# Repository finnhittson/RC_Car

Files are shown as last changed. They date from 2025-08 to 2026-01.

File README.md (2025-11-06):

# 9V Battery Power RC Car
This repo documents how to make an RC car and transmitter using 3D printted parts, a PIC16LF18325 microcontroller, nRF24L01 RF modules, a 9V battery to power the car and the transmitter, and other basic hardware components.

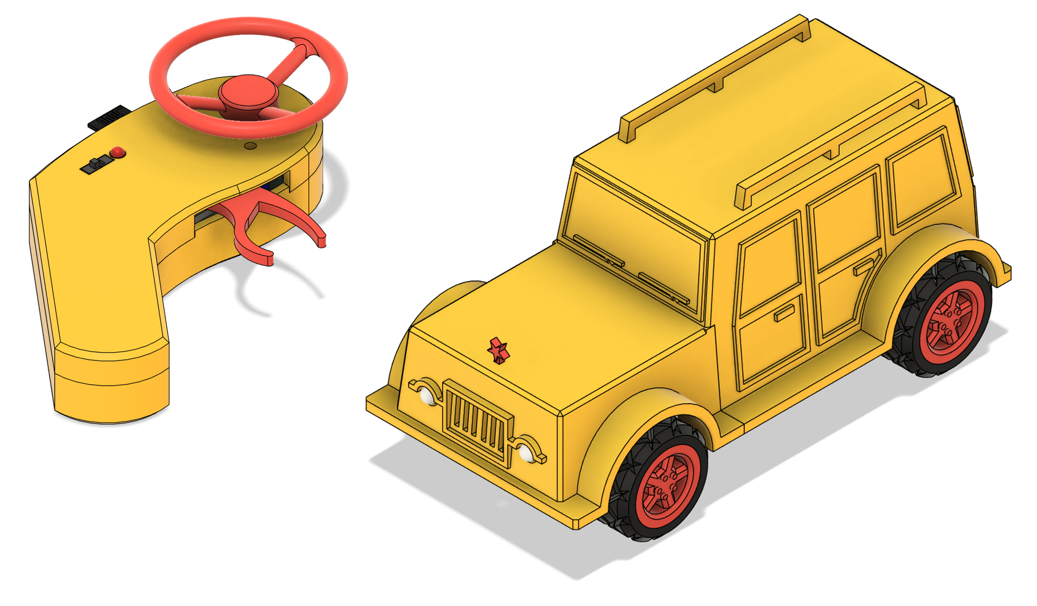
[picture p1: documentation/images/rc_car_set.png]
RC_Car


Table of contents:  
1. [Design Overview](##design-overview)
2. [Software](###software)
3. [Electrical](###electrical)
4. [Bill of Materials](##bill-of-materials)
## Design Overview
The three main components in building this car are the software, electrical, and the mechanical aspect of the car and controller. The following sections talks about each of these parts in detail.

### Software
Using the PIC16LF18326 as the microcontroller, the driver code was written exclusively in C. The driver code was programmed onto the PIC16 using the MPLAB SNAP and the MPLABX IDE. The software components are broken into the following three files:
1. `main.c`: runs main finite state machine responsible for executing high level transmitter/receiver instructions for controlling motors and servos for the receiver and reading analog control inputs for the trasmitter.
2. `spi.c`: helper SPI functions for transmitting and receiving messages to and from the nRF24L01 radio module.
3. `nRF24L01.c`: helper functions for configuring the nRF24L01 radio module using the `spi.c` functons.

Because this project is intended to be a workshop only one version of code or `main.c` file is written for simplicity. Therefore, for the `main.c` to differentiate between running transmitter code and receiver, a GPIO pin on the micro is dedicated for this indication. The pin under questions is RA5 (pin 2) from the tables below which descripe the pinout for the PIC16 in both the receiver and transmitter. If RA5 is pulled high, then the `main.c` executes transmitter code only. Similarly if RA5 is pulled low, then the `main.c` only executes receiver code. 

| Transmitter Pin Description | | | | | | Receiver Pin Description | | | |
|---|---|---|---|-|-|---|---|---|---|
| **Pin Number** | **Port** | **Net Name** | **Notes** | | | **Pin Number** | **Port** | **Net Name** | **Notes** |
| 1 | $V_{DD}$ | 3.3V | power supply | | | 1 | $V_{DD}$ | 3.3V | power supply |
| 2 | RA5 | 3.3V | type select | | | 2 | RA5 | GND | type select |
| 3 | RA4 | CSN | SPI bus | | | 3 | RA4 | CSN | SPI bus |
| 4 | RA3 | MCLR | program/NC | | | 4 | RA3 | MCLR | program/NC |
| 5 | RC5 | MOSI | SPI bus | | | 5 | RC5 | CE | radio enable |
| 6 | RC4 | SPEED | pot input | | | 6 | RC4 | PWM5.1 | motor PWM |
| 7 | RC3 | STEER | pot input | | | 7 | RC3 | PWM6 | servo PWM |
| | | | | | | | | | |
| 8 | RC2 | IRQ | radio interrupt | | | 8 | RC2 | PWM5 | motor PWM |
| 9 | RC1 | MISO | SPI bus | | | 9 | RC1 | MISO | SPI bus |
| 10 | RC0 | SCK | SPI bus | | | 10 | RC0 | SCK | SPI bus |
| 11 | RA2 | CE | radio enable | | | 11 | RA2 | MOSI | SPI bus |
| 12 | RA1 | STEER_TRIM | pot input | | | 12 | RA1 | IRQ | radio interrupt |
| 13 | RA0 | LED | status | | | 13 | RA0 | LIGHTS | status |
| 14 | $V_{SS}$ | GND | power supply | | | 14 | $V_{SS}$ | GND | power supply |

The following image shows the state machine executed on the transmitter PIC16. When the PIC16 detects its a transmitter then it starts the state machine with the inital state of *COLLECT_ADC_DATA*. In the *COLLECT_ADC_DATA* state, the PIC16 cycles through the three ADC ports to collect their value. Once complete, it transitions to the *TRANSMIT_ADC_DATA* state where it packages up this information into a packet and sents this information over the SPI bus to the nRF24L01 radio module. Once this is complete it then transitions to the *CLEAR_INTERRUPT* state. In this state the PIC16 is waiting for the interrupt line to go low which indicates a successful transmission to the receiver. From here the state machine then transitions to a *DONE* state where the hardware to read the analog pins is reinitialized and the process repeates itself after *DONE* transitions to *COLLECT_ADC_DATA*.

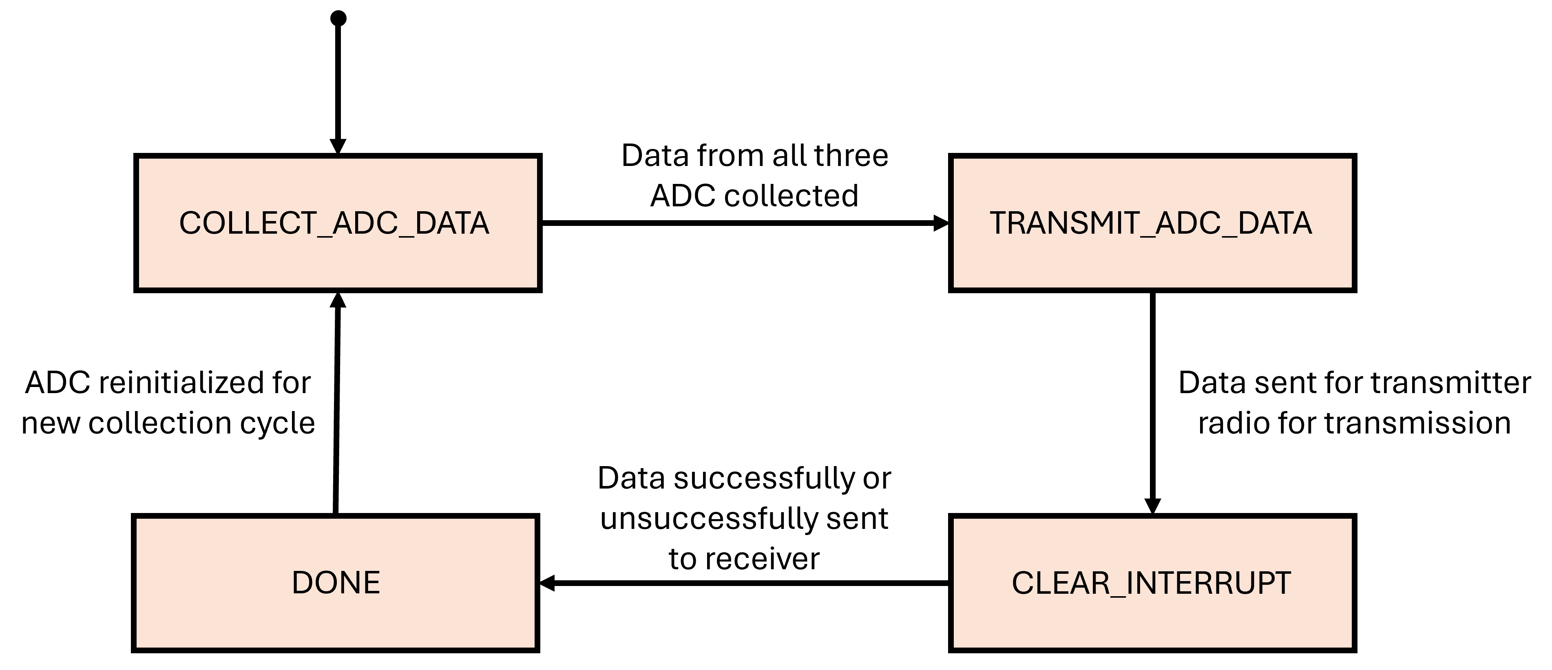
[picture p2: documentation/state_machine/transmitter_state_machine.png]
Transmit_state_machine


The transmission packet is 8 bytes long and has the following breakdown.
1. Byte 1 is the radio ID and is chosen by the user as an extra indentification method so that in the instance when the radio receives a packet from another RC car on the same channel, it will only execute the instructions if the packet come from a transmitter with the same ID.
2. Byte 2 is the high byte of the ADC conversion value for RC4. The PIC16 has a 10 bit ADC so it takes two bytes to store its value. It stores the eight LSB of the conversion in the first byte and the remaining two bits in the first two bits of the second byte.
3. Byte 3 is the low byte of the ADC conversion value for RC4.
4. Byte 4 is the high byte of the ADC conversion value for RC3.
5. Byte 5 is the low byte of the ADC conversion value for RC3.
6. Byte 6 is the high byte of the ADC conversion value for RA1.
7. Byte 7 is the low byte of the ADC conversion value for RA2.
8. Byte 8 is a checksum of all the bytes transmitted. The checksum is computed by summing all the bytes and subtracting the result from 0xFF. The result is transmitted and the receiver checks the checksum by summing every byte of the packet and if the result is 0xFF then no bits were corrupted or lost.

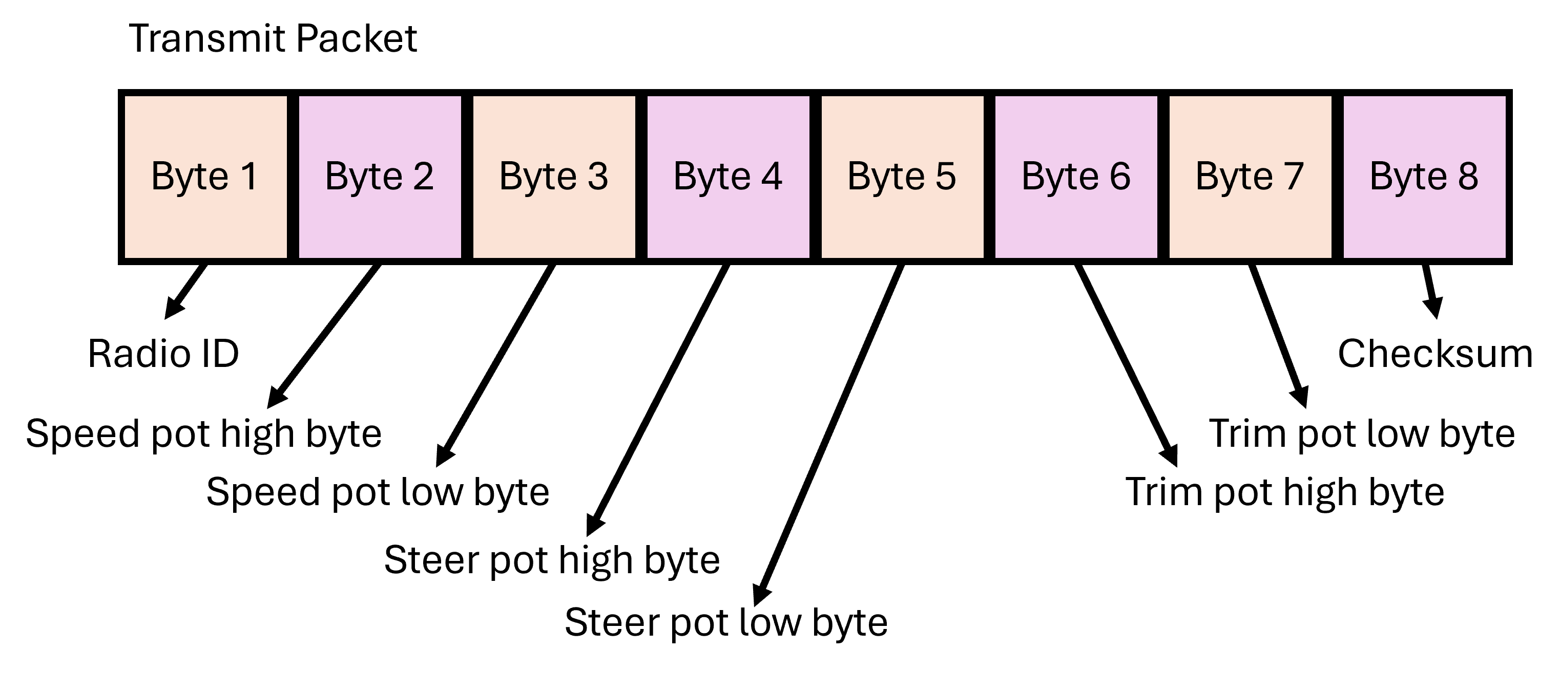
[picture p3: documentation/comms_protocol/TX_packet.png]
Packet_structure


When the PIC16 detects is a receiver it starts the state machine in the *READ_RX*. In this state it waits until the interrupt line from the nRF24L01 radio module goes low which indicates that a packet has been received. From here it transitions to the *UPDATE_CONTROLS* state. In this state the PIC16 collects the packet from the nRF24L01 radio module, unpacks it, and updates the PWM signals for the servo and motor. Once complete it transitions back to the *READ_RX* state where it waits until the next packet is ready.

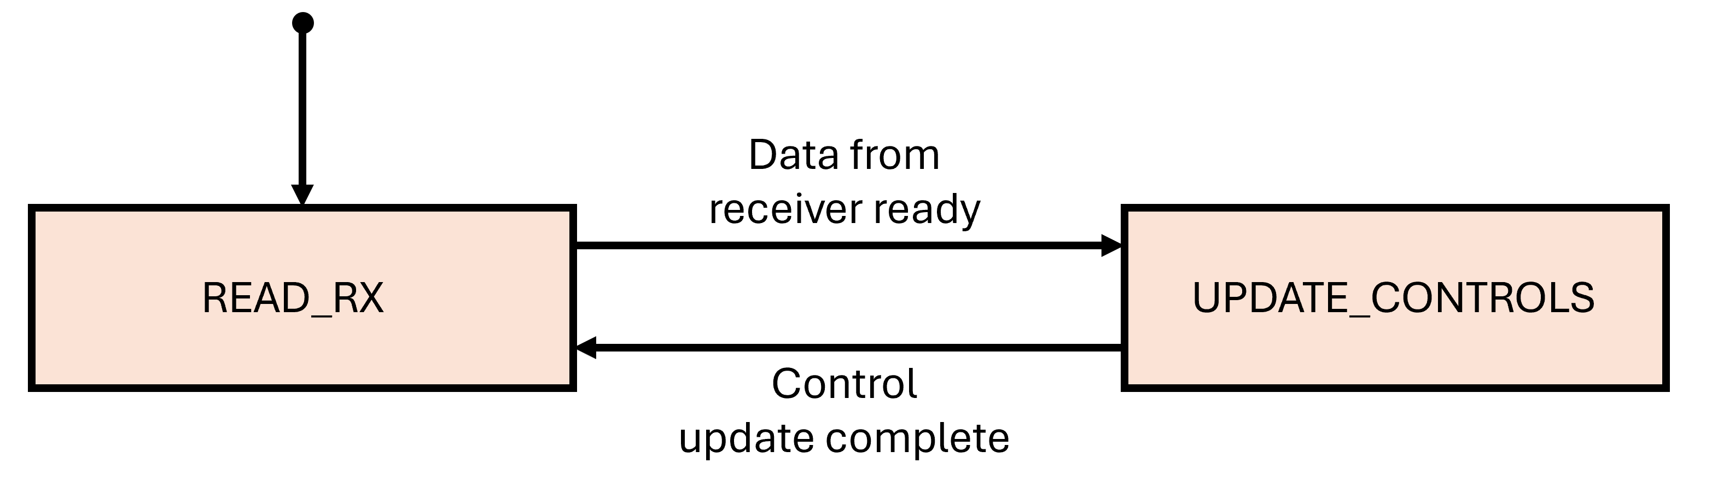
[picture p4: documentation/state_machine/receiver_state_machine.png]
Receive_state_diagram

### Electrical
The receiver schematic is shown below. For the receiver, the PIC16LF18325 communicates with the nRF24L01 radio module through a SPI bus for receiving commands that are then decoded into a PWM signals for motor and servo control. The PIC16 also controls the motors and servo respectivly and was chosen for its small size, GPIO pin count, and packaging style. The L9110 h-bridge controls the motor and is a very basic h-bridge for driving small motors which make it perfect for this application. The LM2937 linear voltage regulator creates the 3.3V supply for the PIC16, nRF24L01 radio module, lights, and servo power. The lights part of the schematic act as the headlights of the car and are controlled by the PIC16 toggeling the 2N7000 mosfets. 
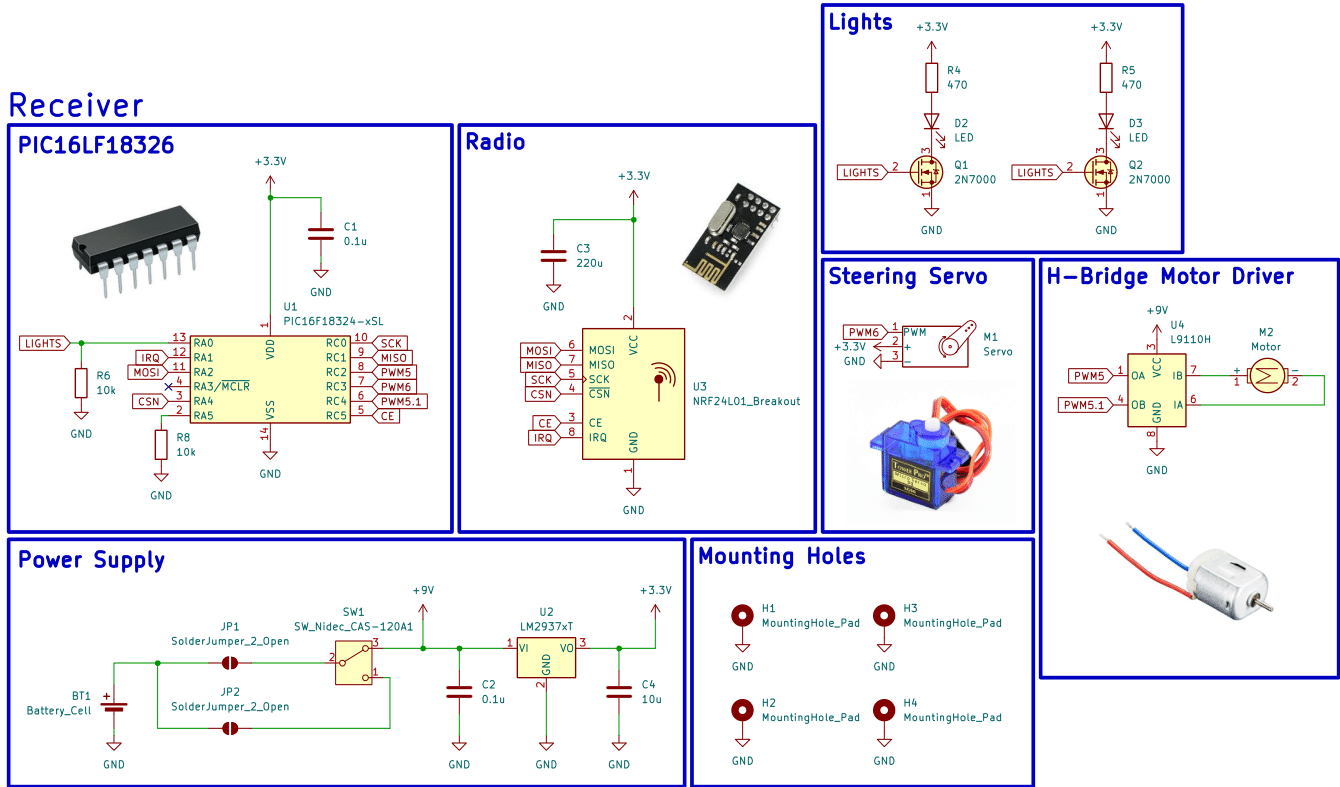
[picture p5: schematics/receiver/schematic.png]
Receiver_schematic


The transmitter schematic is shown below. In this instance the PIC16 commuicates with the nRF24L01 radio module to send commands for the receiver. The PIC16 also controls the status LED which indicates power and pairing status. The two modes of control are the two potentiometers which act as the cars accelerator and steering control. There is also one trim pot for the driver to tune the front steering axel so that the car does not drift left or right when driving straight.

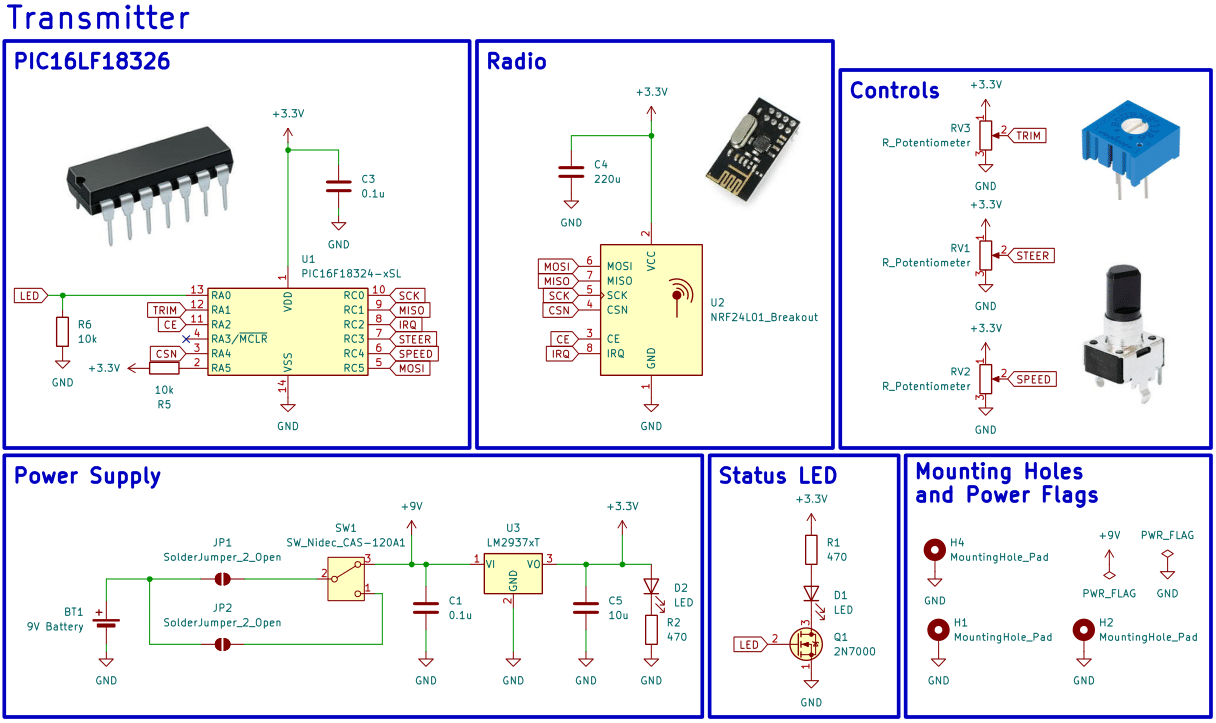
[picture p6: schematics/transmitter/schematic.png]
Transmitter_schematic


### Mechanical

## Bill of Materials
| Transmitter Bill of Materials | | | |
|---|---|---|---|
| **Component** | **Quantity** | **Source** | **Part Number** |
| 9V battery | 1 | DigiKey | 547-A1604BK210J-ND |
| 0.1uF | 2 | DigiKey | BC1084TR-ND |
| 220uF | 1 | DigiKey | 399-6122-ND |
| 10uF | 1 | DigiKey | 399-15738-ND |
| LED | 2 | DigiKey | 732-5016-ND |
| 2N7000 | 1 | DigiKey | 4878-2N7000CT-ND |
| 470 | 2 | DigiKey | CF14JT470RTR-ND |
| 10k | 2 | DigiKey | CF14JT10K0TR-ND |
| 5k Control Pot | 2 | DigiKey | 2223-PT01-D115D-B502-ND |
| 5k Trim Pot | 1 | DigiKey | 3386P-103LF-ND |
| Power Switch | 1 | DigiKey | EG1903-ND |
| PIC16LF18326 | 1 | DigiKey | PIC16LF18326-I/P-ND |
| nRF24L01 Radio Module | 1 | AliExpress | [nRF24L01](https://www.aliexpress.us/item/3256809251216534.html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) |
| LM2937 | 1 | DigiKey | LM2937ET-3.3/NOPB-ND |

| Receiver Bill of Materials | | | |
|---|---|---|---|
| **Component** | **Quantity** | **Source** | **Part Number** |
| 9V battery connector | 1 | DigiKey | 547-A1604BK210J-ND |
| 0.1uF | 2 | DigiKey | BC1084TR-ND |
| 220uF | 1 | DigiKey | 399-6122-ND |
| 10uF | 1 | DigiKey | 399-15738-ND |
| LED | 2 | DigiKey | 732-5016-ND |
| 9g Servo | 2 | DigiKey | 732-5016-ND |
| 2N7000 | 1 | DigiKey | 4878-2N7000CT-ND |
| 470 | 2 | DigiKey | CF14JT470RTR-ND |
| 10k | 2 | DigiKey | CF14JT10K0TR-ND |
| Power Switch | 1 | DigiKey | EG1903-ND |
| PIC16LF18326 | 1 | DigiKey | PIC16LF18326-I/P-ND |
| nRF24L01 Radio Module | 1 | AliExpress | [nRF24L01](https://www.aliexpress.us/item/3256809251216534.html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) |
| LM2937 | 1 | DigiKey | LM2937ET-3.3/NOPB-ND |
| L9110H | 1 | DigiKey | 1528-4489-ND |

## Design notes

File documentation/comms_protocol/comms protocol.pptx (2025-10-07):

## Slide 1

Transmit Packet

Byte 1

Radio ID

Byte 2

Byte 3

Byte 4

Byte 5

Byte 6

Byte 7

Byte 8

Checksum

Speed pot high byte

Speed pot low byte

Trim pot high byte

Trim pot low byte

Steer pot high byte

Steer pot low byte

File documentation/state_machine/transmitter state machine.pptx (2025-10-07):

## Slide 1

COLLECT_ADC_DATA

Data from all three
ADC collected

TRANSMIT_ADC_DATA

ADC reinitialized for
new collection cycle

Data sent for transmitter
radio for transmission

DONE

Data successfully or
unsuccessfully sent
to receiver

CLEAR_INTERRUPT

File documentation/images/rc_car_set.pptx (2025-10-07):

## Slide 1

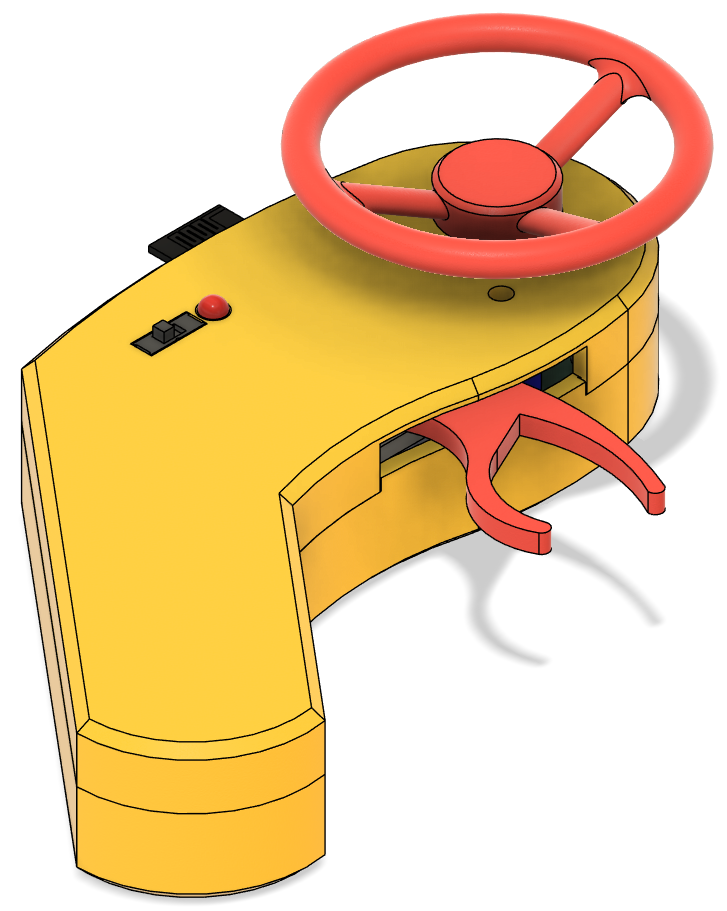
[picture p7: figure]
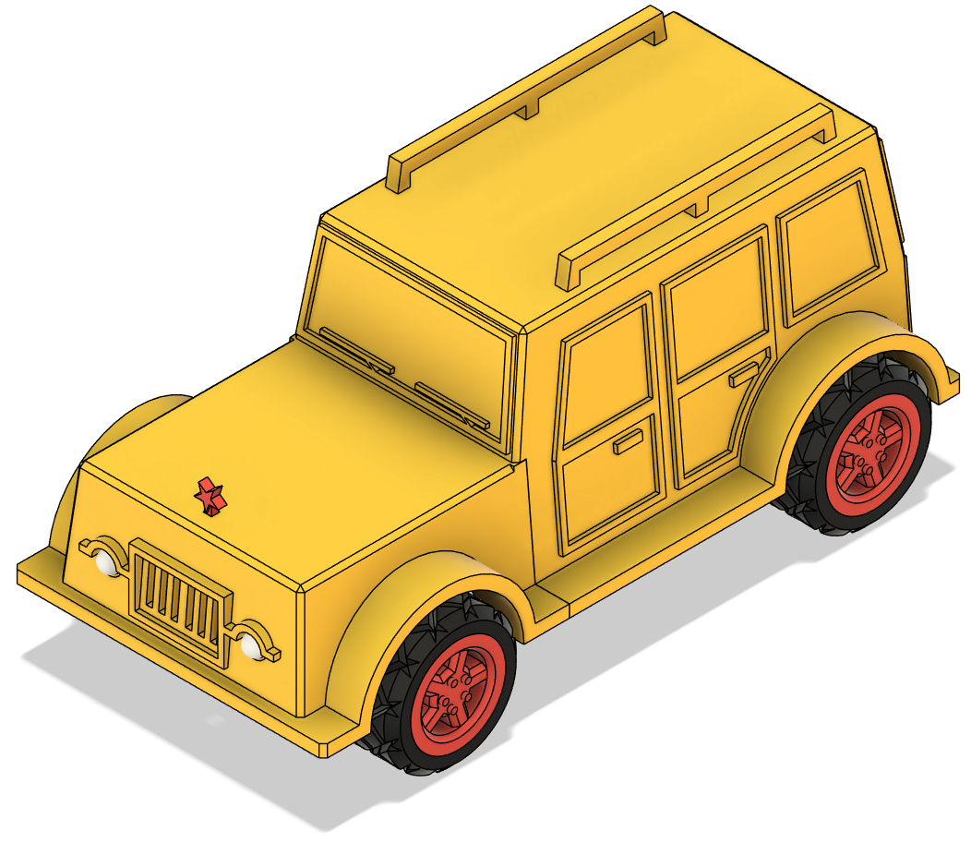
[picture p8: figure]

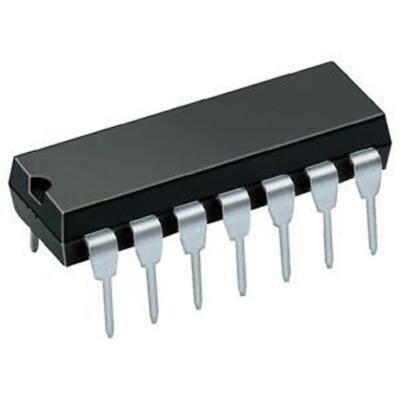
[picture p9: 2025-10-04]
schematics/transmitter/images/14 pin dip package.jpg

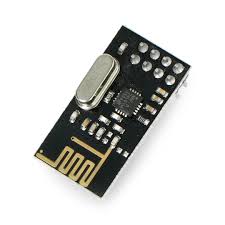
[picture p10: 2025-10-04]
schematics/receiver/images/nRF24L01.jpg

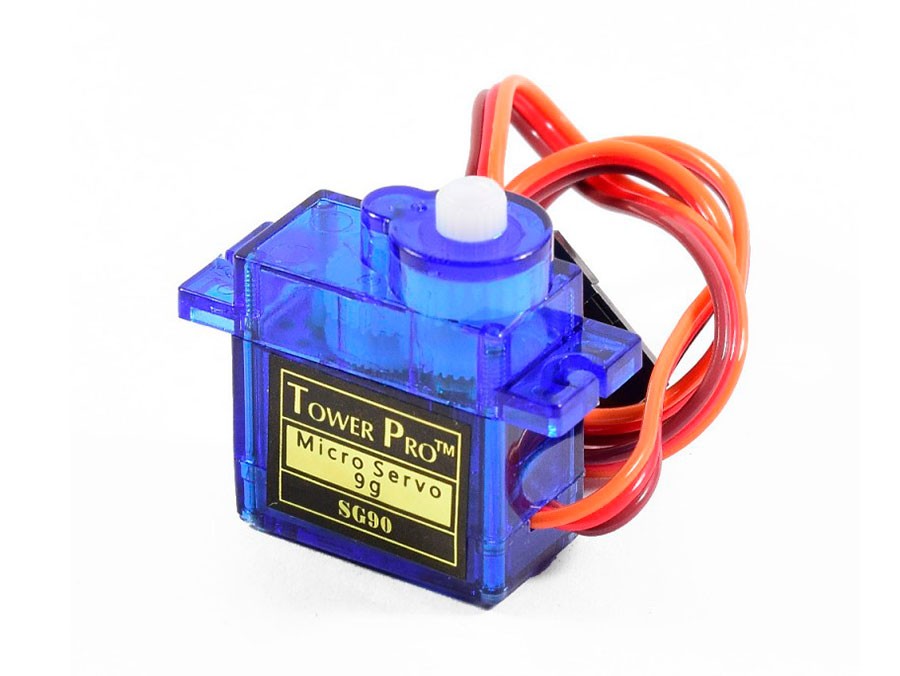
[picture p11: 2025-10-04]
schematics/receiver/images/servo.jpg

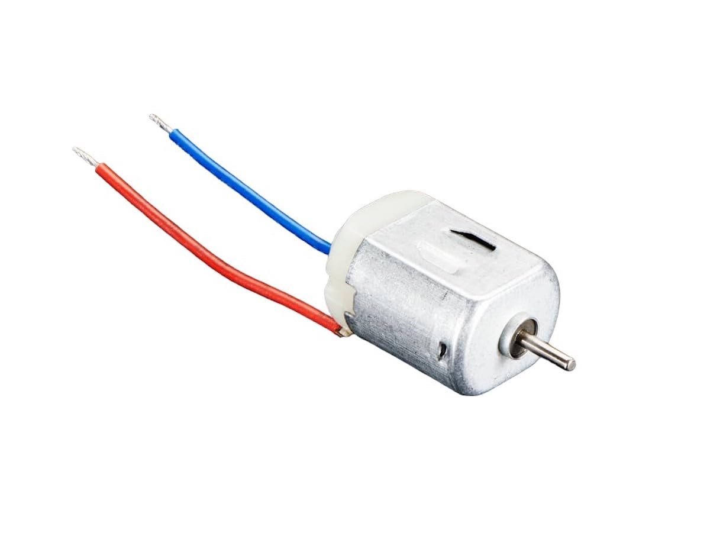
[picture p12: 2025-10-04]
schematics/receiver/images/motor.jpg

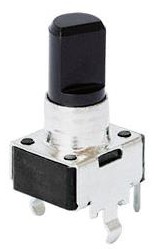
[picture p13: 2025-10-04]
schematics/transmitter/images/control pot.jpg

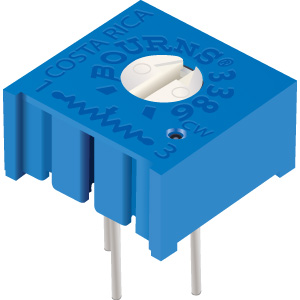
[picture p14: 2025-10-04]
schematics/transmitter/images/trim pot.jpg

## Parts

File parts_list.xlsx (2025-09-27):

McMaster-Carr Parts List
 |  |  |  |  |  | (as of 9/13/2025)
Part | Part Number | Description | Link | Price | Quantity | Amt per Build | Cost per Build
Rotary shaft | 1327K113 | 1/4" diameter, 3" long | https://www.mcmaster.com/products/axle-shafts/rotary-shafts-5/length~3/diameter~1-4-1/ | $4.10 | 1 | 1 | $4.10
Clevis pin | 90378A112 | 1/8" diameter, 7/16" length | https://www.mcmaster.com/products/lock-pins/clevis-pins-4~/clevis-pins-3~~/diameter~1-8-1/usable-length~7-16/ | $3.67 | 1 | 2 | $7.34
Cotter pin | 98335A029 | for 7/64" to 9/64" clevis pin diameter | https://www.mcmaster.com/products/cotter-pins/hairpin-cotter-pins-1~~/ | $16.23 | 100 | 2 | $0.32
Music wire | 8908K42 | 0.039" diameter, 1' length | https://www.mcmaster.com/products/music-wire/length~1-ft/diameter~0-039/ | $22.12 | 100 | 1 | $0.22
Extension springs | 9654K944 | 0.5" length, 0.188" outer diameter | https://www.mcmaster.com/products/tension-springs/extension-springs-1~/extension-springs-with-loop-ends-7/od~0-188/length~0-5/ | $11.50 | 12 | 2 | $1.92
Screw | 91290A053 | M2.5, 14mm long | https://www.mcmaster.com/products/screws/socket-head-screws-2~/alloy-steel-socket-head-screws-8/system-of-measurement~metric/thread-size~m2-5/length~14-mm/ | $7.52 | 50 | 3 | $0.45
Heat-Set insert | 94180A323 | M2.5, 5.6mm length | https://www.mcmaster.com/products/inserts/threaded-insert-type~heat-set/tapered-heat-set-inserts-for-plastic-7/system-of-measurement~metric/thread-size~m2-5/ | $24.72 | 100 | 3 | $0.74
 |  |  |  |  |  | Total | $15.10
DigiKey Parts List
Part | Part Number | Description | Link | Price | Quantity | Amt per Build | Cost per Build
Bearing | 1995-1000-ND | 1/4" inner diameter, 5/8 outer diameter | https://www.digikey.com/en/products/detail/mechatronics-bearing-group/R4-2RS/9608359 | $1.92 | 1 | 2 | $3.84
Misc
9V battery
n24LF01

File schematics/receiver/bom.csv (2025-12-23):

Qty | Supplier PN
1 | BH9V-PC-ND
3 | 399-C0402C104K4RACTUTR-ND
1 | 493-2179-2-ND
1 | 1276-1450-2-ND
1 | 490-10516-2-ND
1 | 718-2487-2-ND
4 | 732-5016-ND
2 | 1516-1217-2-ND
2
1 | 1738-1385-ND
1 | 1528-1150-ND
5 | T2N7002AKLMTR-ND
6 | 311-10KJRTR-ND
6 | 311-470JRTR-ND
1 | 311-1.0KJRTR-ND
1 | EG1903-ND
1 | CKN12319-2-ND
1 | https://www.aliexpress.us/item/3256809251216534.html?src=google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
1 | 1528-4489-ND
1 | PIC32MX170F256B-50I/SS-ND
1 | 5272-AMS1117-3.3TR-ND

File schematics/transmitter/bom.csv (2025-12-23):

Qty | Supplier PN
1 | BH9V-PC-ND
1 | 490-10516-2-ND
3 | 399-C0402C104K4RACTUTR-ND
1 | 493-2179-2-ND
1 | 718-2487-2-ND
1 | 1276-1450-2-ND
2 | 1516-1217-2-ND
2
1 | T2N7002AKLMTR-ND
2 | 311-470JRTR-ND
2 | 311-10KJRTR-ND
1 | 311-1.0KJRTR-ND
2 | 2223-PT01-D115D-B502-ND
2 | 3386P-103LF-ND
1 | EG1903-ND
1 | CKN12319-2-ND
1 | https://www.aliexpress.us/item/3256809251216534.html?src=google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
1 | 5272-AMS1117-3.3TR-ND
1 | PIC32MX170F256B-50I/SS-ND

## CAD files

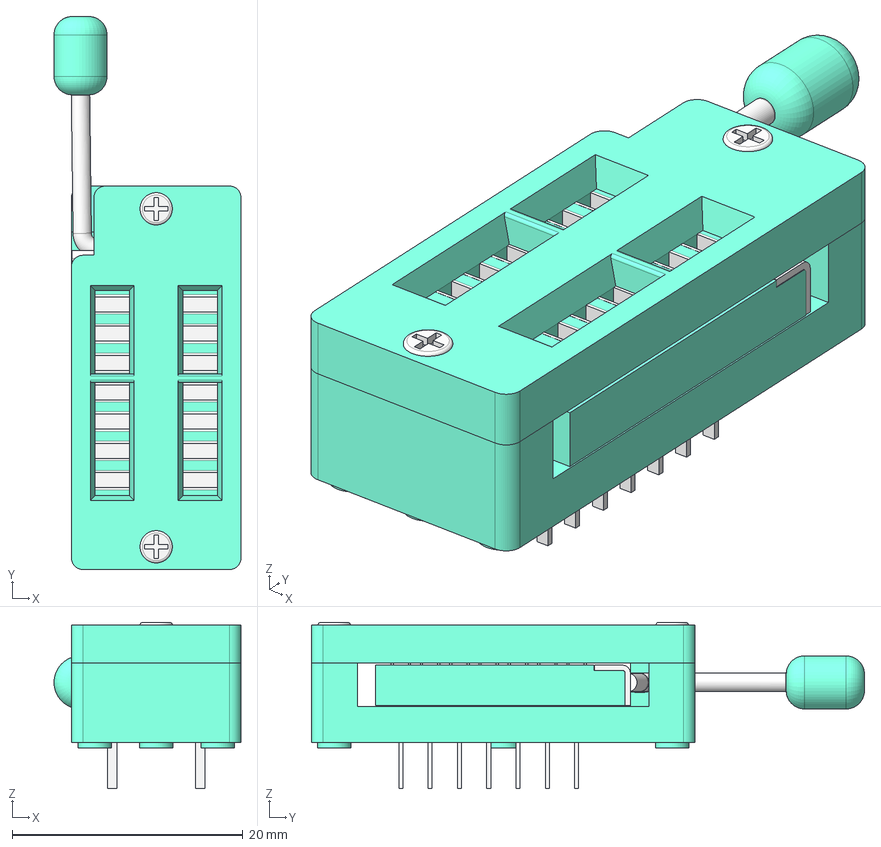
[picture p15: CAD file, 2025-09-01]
schematics/programmer/3d_models/TFXTDOL14-Assy-Down.step
16.2 x 48.0 x 14.4 mm
Slide
Lever
Top
Bottom

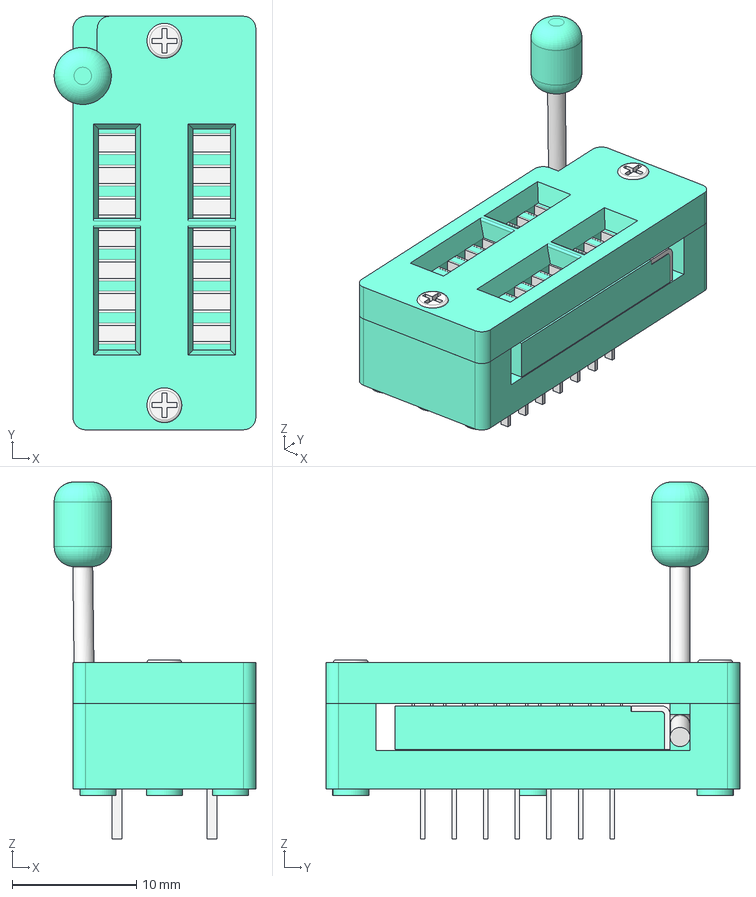
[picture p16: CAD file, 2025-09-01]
schematics/programmer/3d_models/TFXTDOL14-Assy-Up.step
16.2 x 33.2 x 28.7 mm
Slide
Lever
Top
Bottom

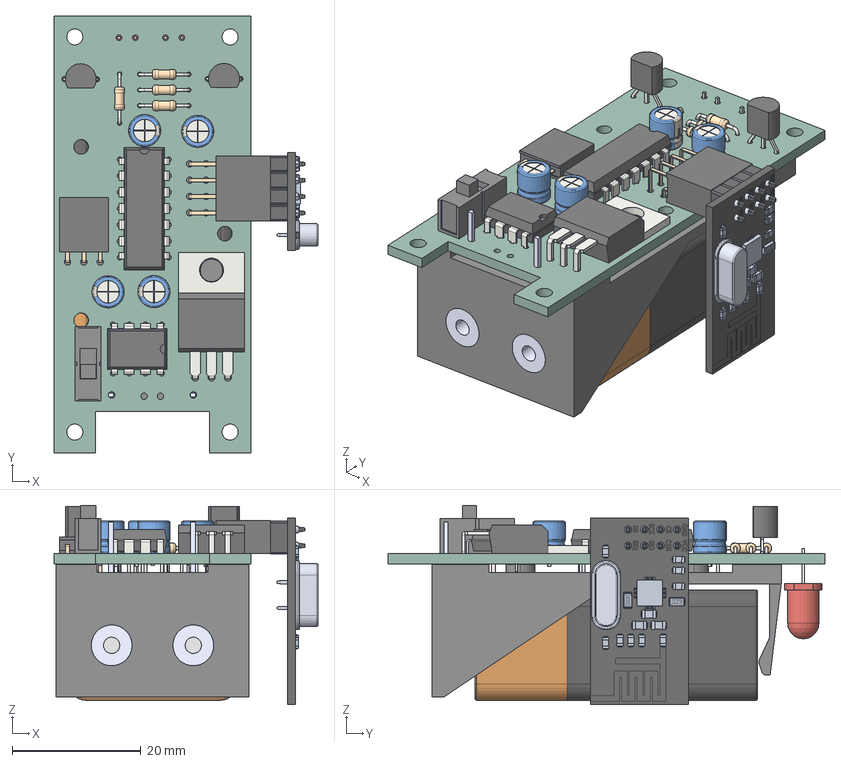
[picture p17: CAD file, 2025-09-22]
schematics/receiver/receiver.step
41.1 x 67.9 x 31.0 mm
R_Axial_DIN0204_L36mm_D16mm_P762mm_Horizontal x 4
CP_Radial_D50mm_P250mm x 4
nRF24L01
PinSocket_2x04_P254mm_Horizontal
TO-220-3_Horizontal_TabDown
DIP-8_W7.62mm
TO-92_Inline_Wide x 2
switch v1
PinSocket_1x03_P254mm_Horizontal
DIP-14_W7.62mm
BH9VPC
layer1[1]
LED_D5.0mm x 2
_autosave-receiver_PCB

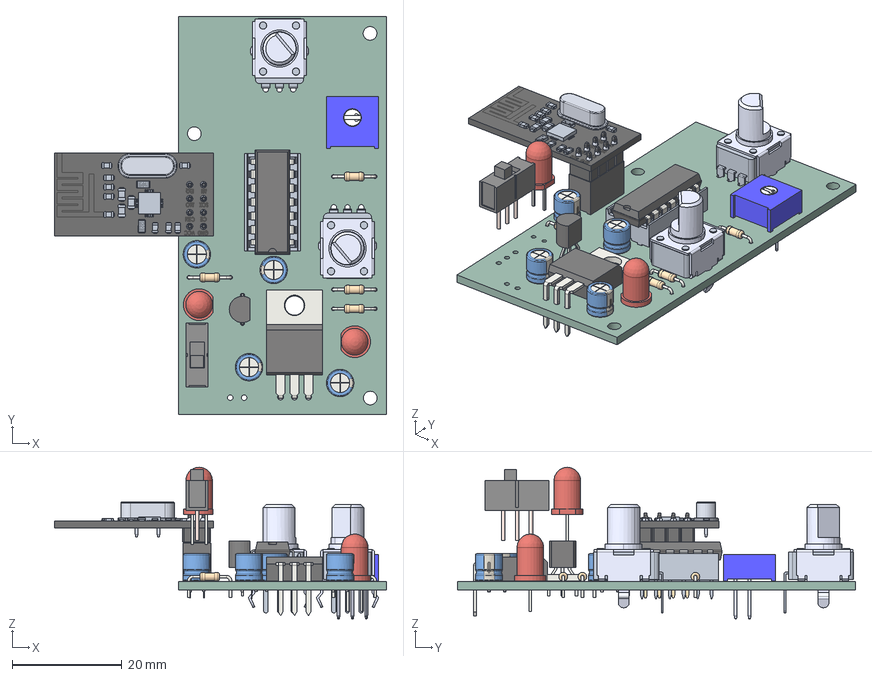
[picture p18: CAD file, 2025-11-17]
schematics/transmitter/transmitter.step
60.6 x 72.6 x 27.6 mm
TO-92_Inline_Wide
CP_Radial_D50mm_P250mm x 4
R_Axial_DIN0204_L36mm_D16mm_P762mm_Horizontal x 4
DIP-14_W7.62mm
3386P-1-100
TO-220-3_Horizontal_TabDown
CUI_DEVICES_PT01-D115D-B502 x 2
switch v1
LED_D5.0mm x 2
nRF24L01
PinSocket_2x04_P254mm_Vertical
_autosave-transmitter_PCB

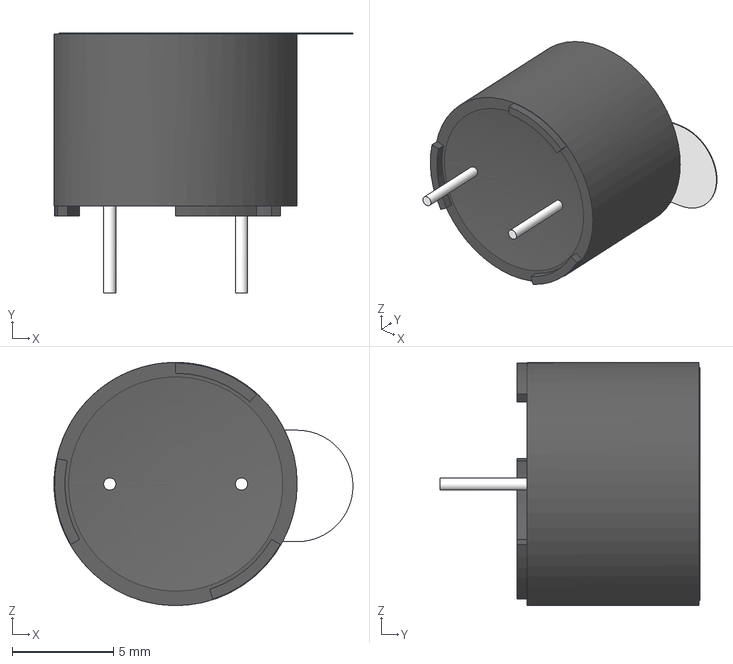
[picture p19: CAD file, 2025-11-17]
schematics/receiver/3d_models/AT-1224-TWT-5V-2-R.step
14.7 x 12.9 x 12.0 mm

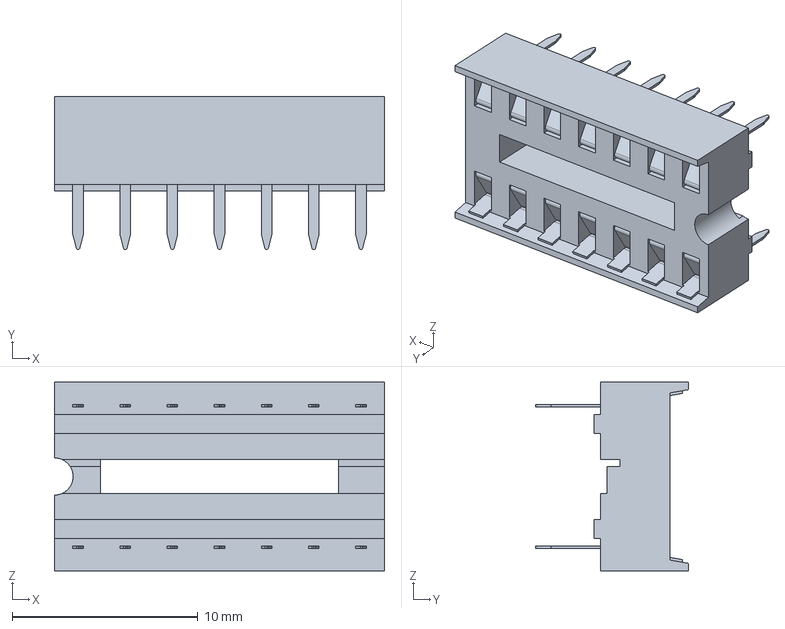
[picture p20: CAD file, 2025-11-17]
schematics/transmitter/3d_models/socket_a_14-lc-tt.stp
17.8 x 8.25 x 10.2 mm

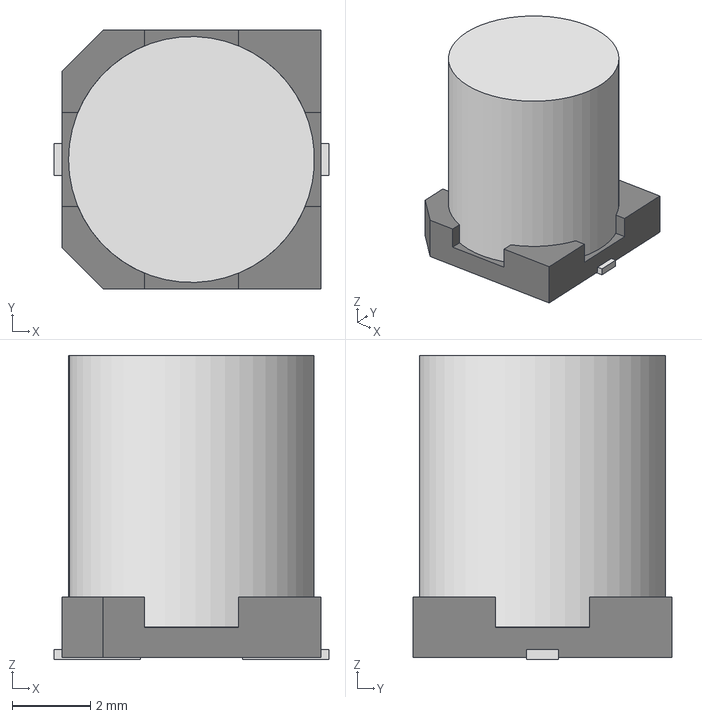
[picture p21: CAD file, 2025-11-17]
schematics/transmitter/3d_models/U2-K_NCH.step
7.01 x 6.60 x 7.75 mm

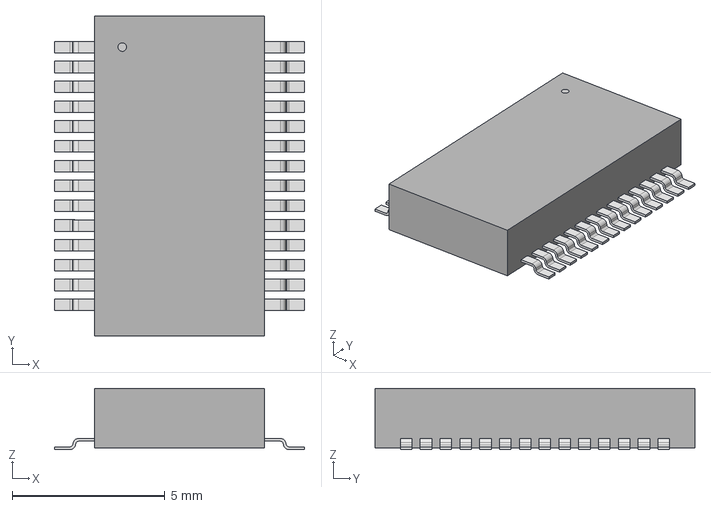
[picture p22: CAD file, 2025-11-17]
schematics/receiver/3d_models/SSOP28_MC_MCH.step
8.20 x 10.5 x 2.01 mm

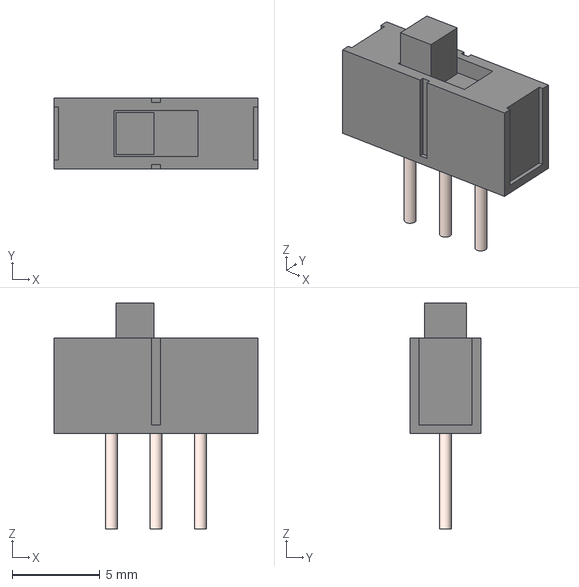
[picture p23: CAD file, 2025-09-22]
schematics/transmitter/3d_models/switch v1.step
11.6 x 4.03 x 12.9 mm

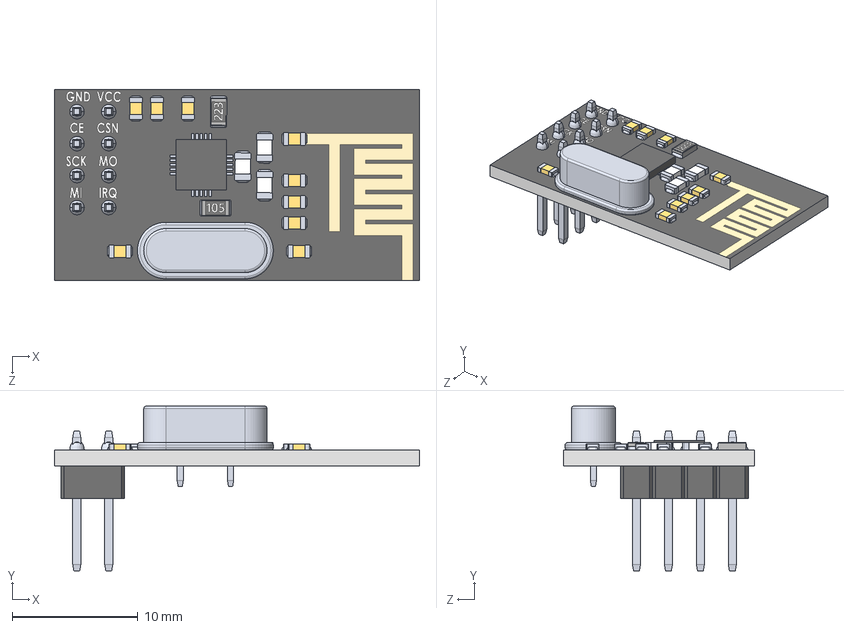
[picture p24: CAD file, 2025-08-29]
schematics/transmitter/3d_models/nRF24L01.STEP
29.0 x 13.1 x 15.2 mm
nrfboard
CrystalOscillator
doubleMaleHeader x 4
solder x 8
1.7mmSmdCeramicCapacitor x 9
smdResistor223
smdResistor105
smdceramiccapacitorwhite x 3
4x4SMDchip

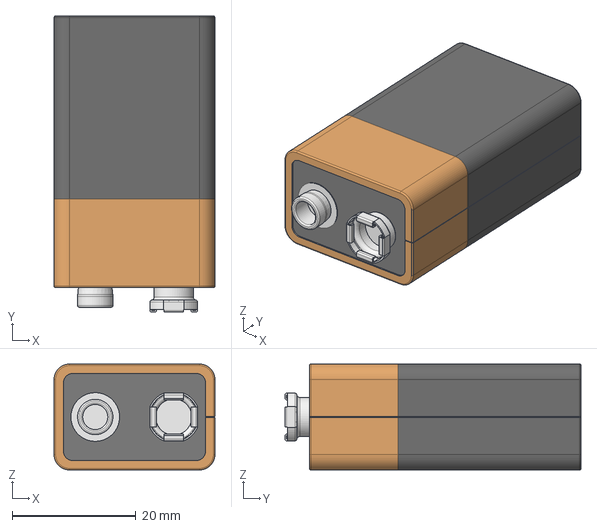
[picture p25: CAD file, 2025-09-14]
schematics/receiver/3d_models/9V-battery.stp
26.0 x 47.9 x 17.1 mm

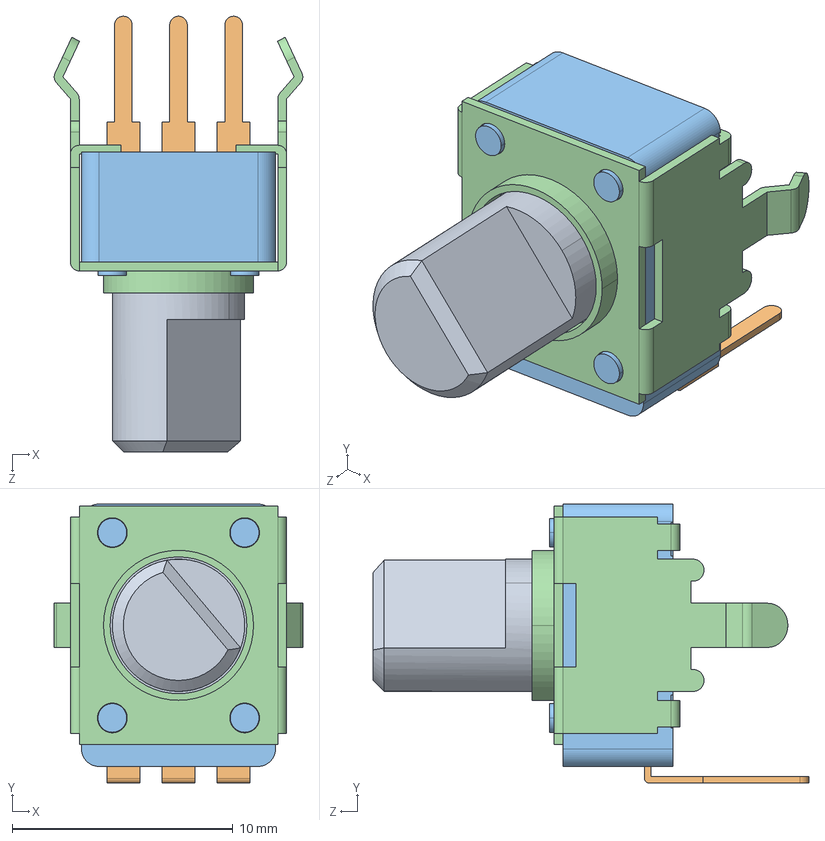
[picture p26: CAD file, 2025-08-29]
schematics/transmitter/3d_models/PT01-D115D-B502.step
11.3 x 12.7 x 19.8 mm
PT01_15D_SHAFT
PT01-D_BODY
PT01-D_SHELL

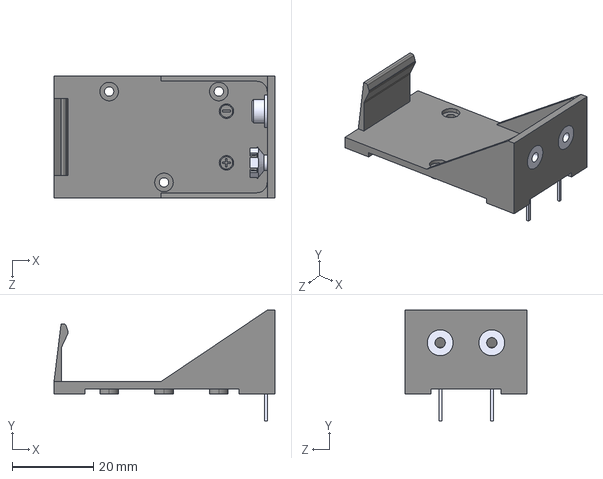
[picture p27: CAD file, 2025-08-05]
schematics/receiver/3d_models/BH9VPC.STEP
54.4 x 27.2 x 30.0 mm

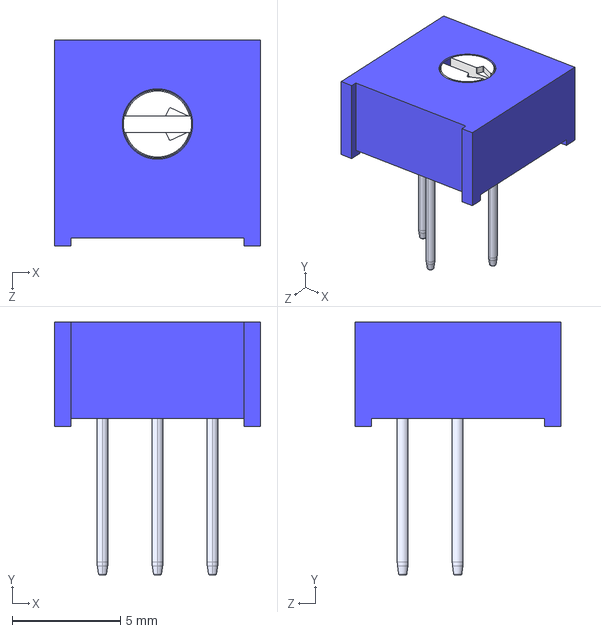
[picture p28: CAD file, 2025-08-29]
schematics/transmitter/3d_models/3386P-1-104LF.STEP
9.53 x 11.7 x 9.53 mm

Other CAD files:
schematics/receiver/3d_models/switch v1.step
schematics/receiver/3d_models/1825910-6.step
schematics/receiver/3d_models/2_screw_terminal.stp
schematics/transmitter/3d_models/1825910-6.step
schematics/transmitter/3d_models/2_screw_terminal.stp

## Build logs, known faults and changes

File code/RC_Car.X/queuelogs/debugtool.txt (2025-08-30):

17025 1756515855851 GEN4_TO_CONTROLLER_LOG:GEN4_DEBUG_INT_LOG_PIC16F18326 Pre:DebugReadTargetMemory
17025 1756515855851 GEN4_TO_CONTROLLER_LOG:GEN4_DEBUG_INT_LOG_PIC16F18326 Payload
17025 1756515855851 GEN4_TO_CONTROLLER_LOG:GEN4_DEBUG_INT_LOG_PIC16F18326 FileRegs
17025 1756515855851 GEN4_TO_CONTROLLER_LOG:GEN4_DEBUG_INT_LOG_PIC16F18326 3
17025 1756515855851 GEN4_TO_CONTROLLER_LOG:GEN4_DEBUG_INT_LOG_PIC16F18326 3
17025 1756515855851 GEN4_TO_CONTROLLER_LOG:GEN4_DEBUG_INT_LOG_PIC16F18326 Length = 1
17025 1756515855851 GEN4_TO_CONTROLLER_LOG:GEN4_DEBUG_INT_LOG_PIC16F18326 Payload End
17025 1756515855851 XXXX 1756515855851, Thread 17025: XXXX 1756515855851, Entering Thread 17025: Commands::runScriptWithUpload, script name = ReadRAM  
17025 1756515855851 XXXX 1756515855851, Thread 17025: XXXX 1756515855851, Entering Thread 17025: ToolCommUsb::readTransfer, sideData is 0x25 bytes long, transferDataLength is 0x1 bytes long  
17025 1756515855852 XXXX 1756515855852, Thread 17025: com.Send returned false 
17025 1756515855852 XXXX 1756515855852, Thread 17025: readTransfer: exception after writeHeaderAndGetAck null 
17025 1756515855852 XXXX 1756515855852, Thread 17025: XXXX 1756515855852, Entering Thread 17025: ToolCommUsb::recoverFromProtocolError, type = NO_SCRIPT  
17025 1756515855852 XXXX 1756515855852, Thread 17025: Send Abort Script Engine Command 
17025 1756515855852 XXXX 1756515855852, Thread 17025: XXXX 1756515855852, Entering Thread 17025: ToolCommUsb::killScriptEngine  
17025 1756515855852 XXXX 1756515855852, Thread 17025: com.Send returned false 
17025 1756515855852 XXXX 1756515855852, Thread 17025: Failed sending Abort Script Engine Command. Set nuclear option = true 
17025 1756515855852 XXXX 1756515855852, Thread 17025: About to nuke 
17025 1756515855852 XXXX 1756515855852, Thread 17025: XXXX 1756515855852, Entering Thread 17025: ToolCommUsb::nuclearOption  
17025 1756515855853 XXXX 1756515855853, Thread 17025: com.Send returned false

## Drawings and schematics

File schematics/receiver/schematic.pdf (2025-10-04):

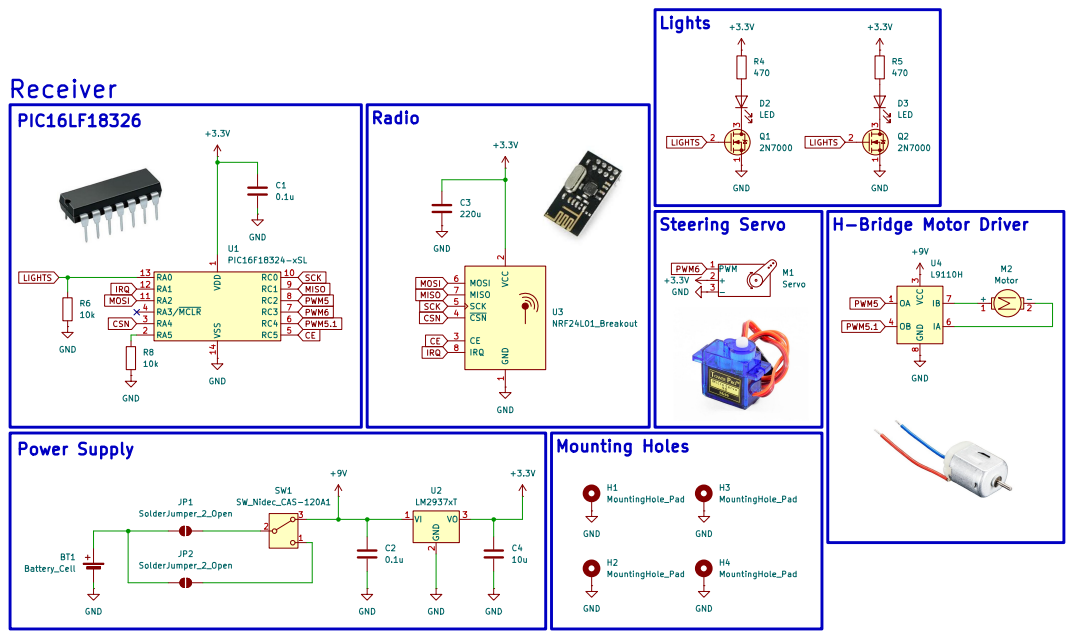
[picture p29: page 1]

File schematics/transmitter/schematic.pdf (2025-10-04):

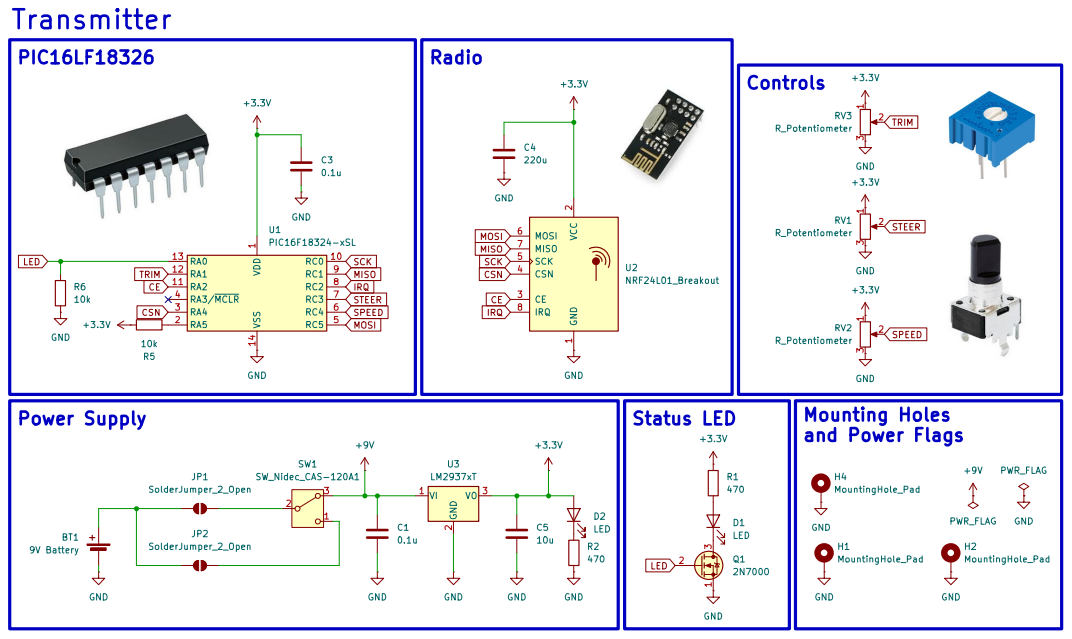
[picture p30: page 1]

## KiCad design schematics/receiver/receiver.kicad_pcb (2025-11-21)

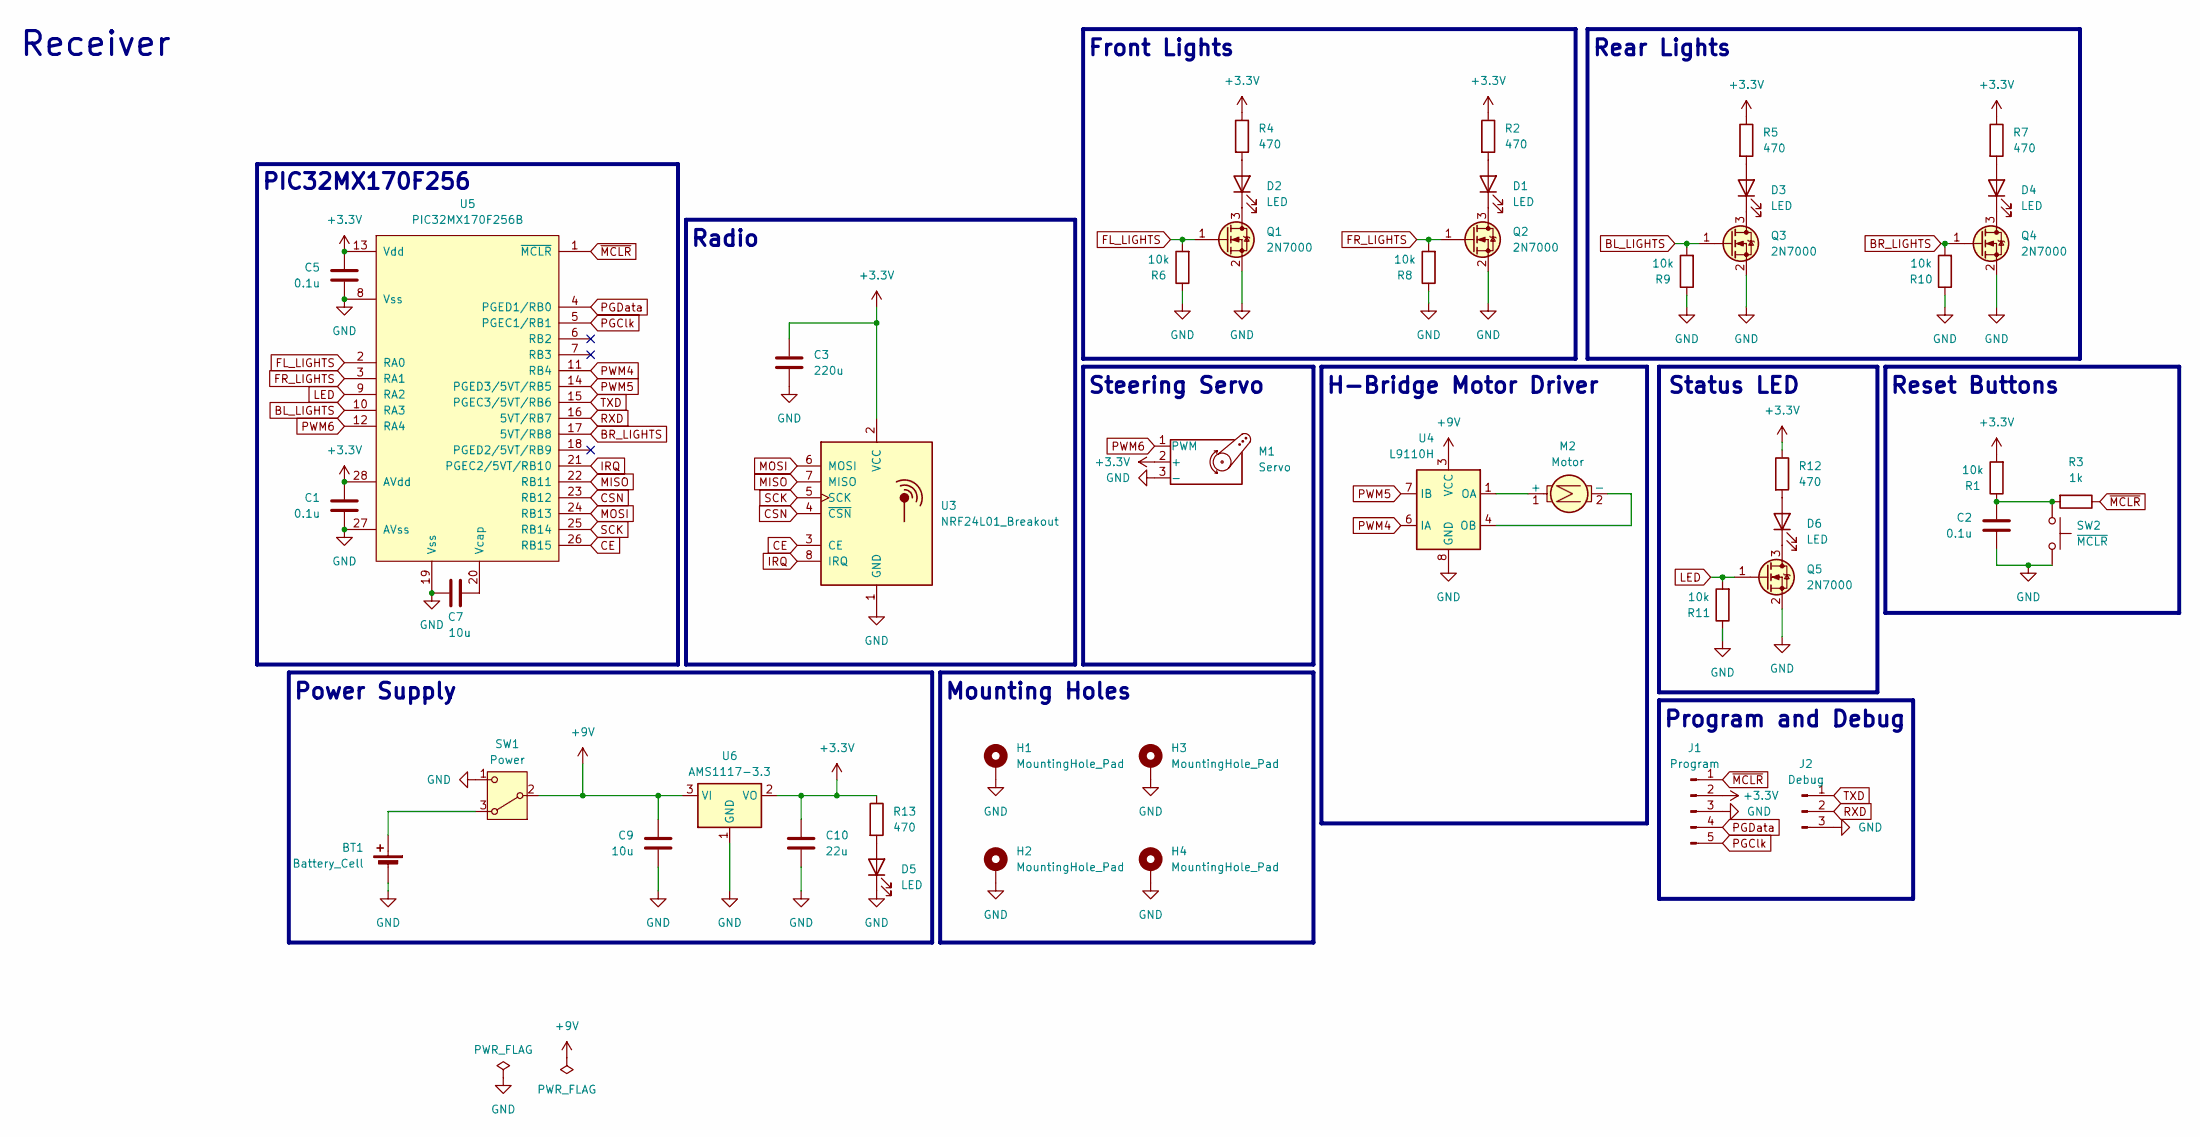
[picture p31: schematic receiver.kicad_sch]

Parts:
BT1: Battery_Cell; BAT_BH9VPC
C1, C2, C5: 0.1u; C_0402_1005Metric
C3: 220u; U2-K_NCH
C7: 10u; C_0402_1005Metric
C9: 10u; C_0805_2012Metric
C10: 22u; CP_EIA-2012-15_AVX-P
D1, D2, D3, D4: LED; PinSocket_1x02_P2.54mm_Vertical
D5, D6: LED; LED_0402_1005Metric
H1, H2, H3, H4: MountingHole_Pad; MountingHole_2.5mm_Pad_TopBottom
J1: Program; PinSocket_1x05_P2.54mm_Vertical
J2: Debug; PinSocket_1x03_P2.54mm_Vertical
M1: Servo; PinSocket_1x03_P2.54mm_Horizontal
M2: Motor; PinSocket_1x02_P2.54mm_Vertical
Q1, Q2, Q3, Q4, Q5: 2N7000; SOT-23
R1, R6, R8, R9, R10, R11: 10k; R_0402_1005Metric
R2, R4, R5, R7, R12, R13: 470; R_0402_1005Metric
R3: 1k; R_0402_1005Metric
SW1: Power; PinSocket_1x03_P2.54mm_Vertical
SW2: ~{MCLR}; SW_1825910-6-4
U3: NRF24L01_Breakout; nRF24L01_Breakout
U4: L9110H; DIP-8_W7.62mm_Socket
U5: PIC32MX170F256B; SSOP28_MC_MCH
U6: AMS1117-3.3; SOT-223-3_TabPin2

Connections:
+3.3V: C1.2, C3.1, C5.2, C10.1, J1.2, M1.2 (+), R1.2, R2.1, R4.1, R5.1, R7.1, R12.1, R13.1, U3.2 (VCC), U5.13 (Vdd), U5.28 (AVdd), U6.2 (VO)
+9V: C9.1, SW1.2 (B), U4.2 (VCC), U4.3 (VCC), U6.3 (VI)
BL_LIGHTS: Q3.1 (G), R9.2, U5.10 (RA3)
BR_LIGHTS: Q4.1 (G), R10.2, U5.17 (5VT/RB8)
CE: U3.3 (CE), U5.26 (RB15)
CSN: U3.4 (~CSN), U5.23 (RB12)
FL_LIGHTS: Q1.1 (G), R6.2, U5.2 (RA0)
FR_LIGHTS: Q2.1 (G), R8.2, U5.3 (RA1)
GND: BT1.2 (-), C1.1, C2.1, C3.2, C5.1, C7.2, C9.2, C10.2, D5.1 (K), H1.1, H2.1, H3.1, H4.1, J1.3, J2.3, M1.3 (-), Q1.2 (S), Q2.2 (S), Q3.2 (S), Q4.2 (S), Q5.2 (S), R6.1, R8.1, R9.1, R10.1, R11.1, SW1.1 (C), SW2.3, SW2.4, U3.1 (GND), U4.5 (GND), U4.8 (GND), U5.8 (Vss), U5.19 (Vss), U5.27 (AVss), U6.1 (GND)
IRQ: U3.8 (IRQ), U5.21 (PGEC2/5VT/RB10)
LED: Q5.1 (G), R11.2, U5.9 (RA2)
MISO: U3.7 (MISO), U5.22 (RB11)
MOSI: U3.6 (MOSI), U5.24 (RB13)
unnamed: BT1.1 (+), SW1.3 (A)
unnamed: C2.2, R1.1, R3.2, SW2.1, SW2.2
unnamed: D1.2 (A), R2.2
unnamed: D1.1 (K), Q2.3 (D)
unnamed: D2.2 (A), R4.2
unnamed: D2.1 (K), Q1.3 (D)
unnamed: D3.2 (A), R5.2
unnamed: D3.1 (K), Q3.3 (D)
unnamed: D4.2 (A), R7.2
unnamed: D4.1 (K), Q4.3 (D)
unnamed: D5.2 (A), R13.2
unnamed: D6.2 (A), R12.2
unnamed: D6.1 (K), Q5.3 (D)
unnamed: M2.1 (+), U4.1 (OA)
unnamed: M2.2 (-), U4.4 (OB)
unnamed: C7.1, U5.20 (Vcap)
PGClk: J1.5, U5.5 (PGEC1/RB1)
PGData: J1.4, U5.4 (PGED1/RB0)
PWM4: U4.6 (IA), U5.11 (RB4)
PWM5: U4.7 (IB), U5.14 (PGED3/5VT/RB5)
PWM6: M1.1 (PWM), U5.12 (RA4)
RXD: J2.2, U5.16 (5VT/RB7)
SCK: U3.5 (SCK), U5.25 (RB14)
TXD: J2.1, U5.15 (PGEC3/5VT/RB6)
~MCLR: J1.1, R3.1, U5.1 (~MCLR)

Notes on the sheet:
Program and Debug
Power Supply
Rear Lights
Front Lights
PIC32MX170F256
Radio
Status LED
Receiver
H-Bridge Motor Driver
Reset Buttons
Steering Servo
Mounting Holes

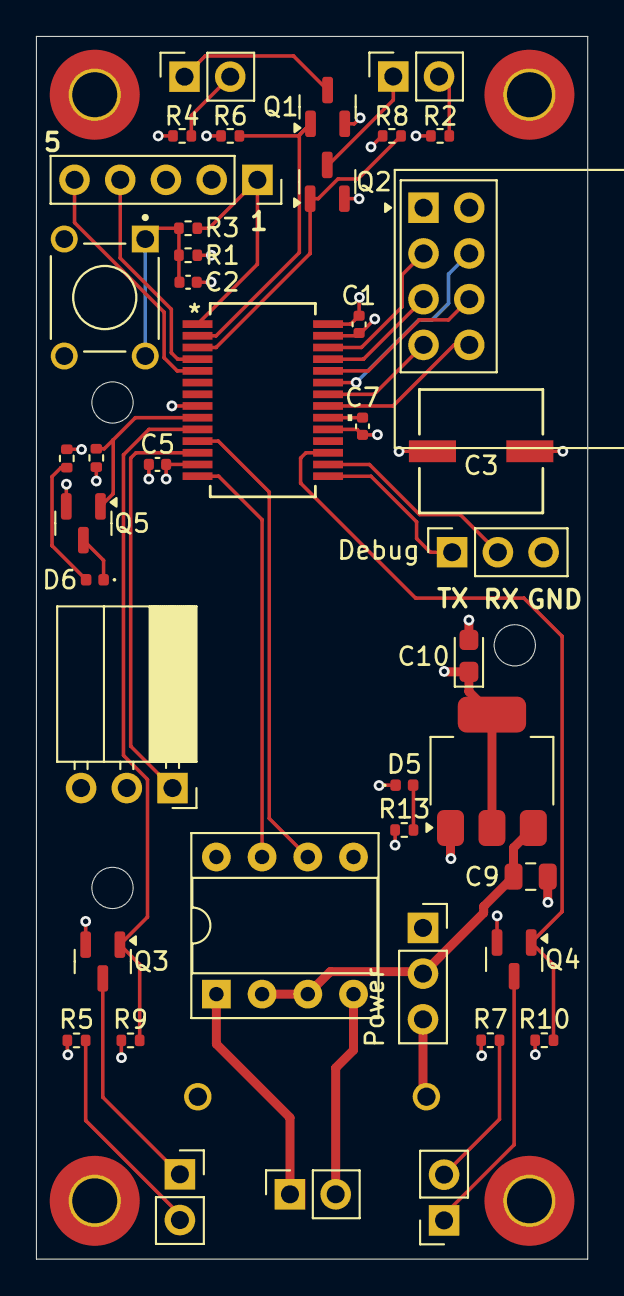
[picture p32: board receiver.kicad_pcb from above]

Board: 4 copper layers, 30.6 x 67.9 mm, 46 parts (1 on the bottom side), 38 nets.

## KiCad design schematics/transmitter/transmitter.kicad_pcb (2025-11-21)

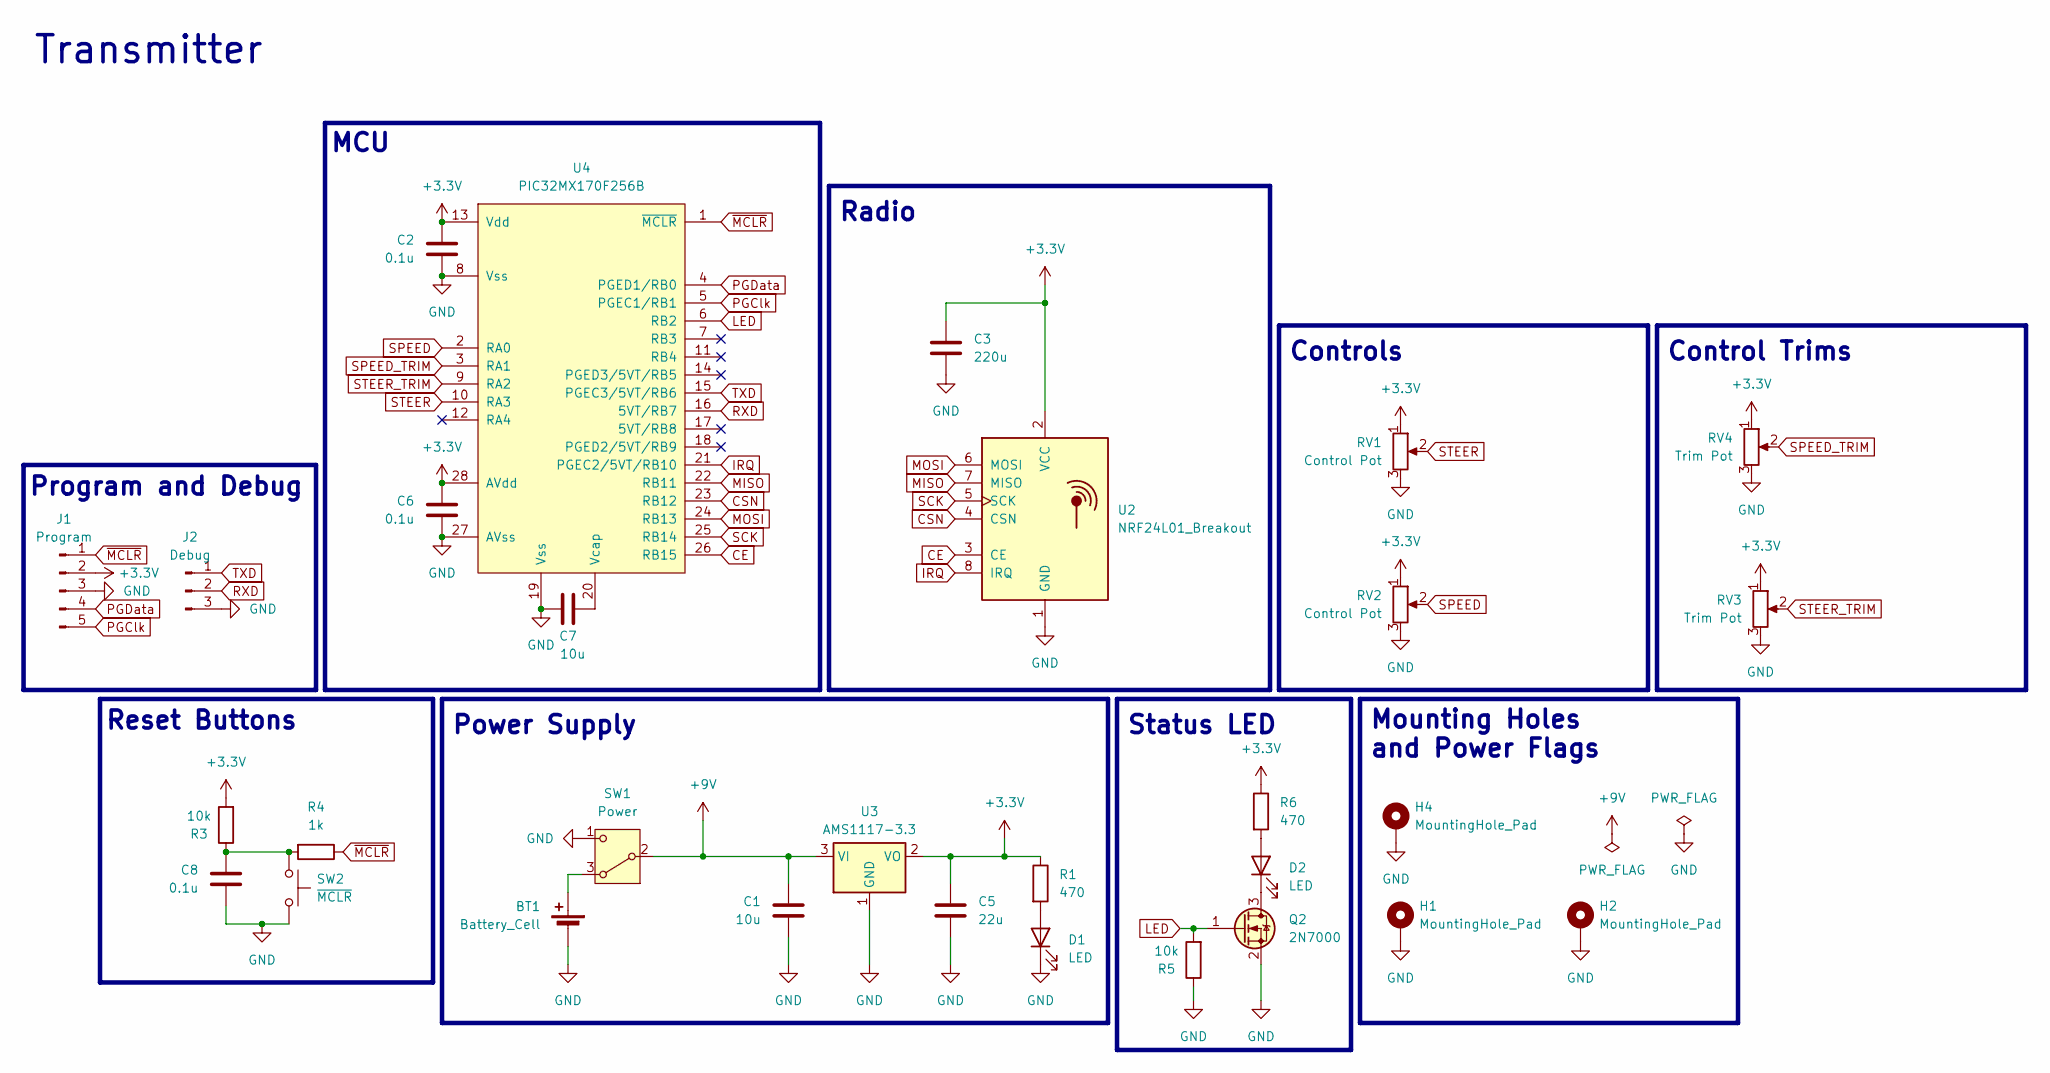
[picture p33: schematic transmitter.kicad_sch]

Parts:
BT1: Battery_Cell; PinSocket_1x02_P2.54mm_Vertical
C1: 10u; C_0805_2012Metric
C2, C6, C8: 0.1u; C_0402_1005Metric
C3: 220u; U2-K_NCH
C5: 22u; CP_EIA-2012-15_AVX-P
C7: 10u; C_0402_1005Metric
D1, D2: LED; LED_0402_1005Metric
H1, H2, H4: MountingHole_Pad; MountingHole_2.5mm_Pad_TopBottom
J1: Program; PinSocket_1x05_P2.54mm_Vertical
J2: Debug; PinSocket_1x03_P2.54mm_Vertical
Q2: 2N7000; SOT-23
R1, R6: 470; R_0402_1005Metric
R3, R5: 10k; R_0402_1005Metric
R4: 1k; R_0402_1005Metric
RV1, RV2: Control Pot; TRIM_PT01-D115D-B502
RV3, RV4: Trim Pot; Potentiometer_Bourns_3386P_Vertical
SW1: Power; PinSocket_1x03_P2.54mm_Vertical
SW2: ~{MCLR}; SW_1825910-6-4
U2: NRF24L01_Breakout; nRF24L01_Breakout
U3: AMS1117-3.3; SOT-223-3_TabPin2
U4: PIC32MX170F256B; SSOP28_MC_MCH

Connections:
+3.3V: C2.2, C3.1, C5.1, C6.2, J1.2, R1.1, R3.2, R6.1, RV1.1, RV2.1, RV3.1, RV4.1, U2.2 (VCC), U3.2 (VO), U4.13 (Vdd), U4.28 (AVdd)
+9V: C1.1, SW1.2 (B), U3.3 (VI)
CE: U2.3 (CE), U4.26 (RB15)
CSN: U2.4 (CSN), U4.23 (RB12)
GND: BT1.2 (-), C1.2, C2.1, C3.2, C5.2, C6.1, C7.2, C8.1, D1.1 (K), H1.1, H2.1, H4.1, J1.3, J2.3, Q2.2 (S), R5.1, RV1.3, RV1.S1, RV1.S2, RV2.3, RV2.S1, RV2.S2, RV3.3, RV4.3, SW1.1 (C), SW2.3, SW2.4, U2.1 (GND), U3.1 (GND), U4.8 (Vss), U4.19 (Vss), U4.27 (AVss)
IRQ: U2.8 (IRQ), U4.21 (PGEC2/5VT/RB10)
LED: Q2.1 (G), R5.2, U4.6 (RB2)
MISO: U2.7 (MISO), U4.22 (RB11)
MOSI: U2.6 (MOSI), U4.24 (RB13)
unnamed: BT1.1 (+), SW1.3 (A)
unnamed: C8.2, R3.1, R4.2, SW2.1, SW2.2
unnamed: D1.2 (A), R1.2
unnamed: D2.2 (A), R6.2
unnamed: D2.1 (K), Q2.3 (D)
unnamed: C7.1, U4.20 (Vcap)
PGClk: J1.5, U4.5 (PGEC1/RB1)
PGData: J1.4, U4.4 (PGED1/RB0)
RXD: J2.2, U4.16 (5VT/RB7)
SCK: U2.5 (SCK), U4.25 (RB14)
SPEED: RV2.2, U4.2 (RA0)
SPEED_TRIM: RV4.2, U4.3 (RA1)
STEER: RV1.2, U4.10 (RA3)
STEER_TRIM: RV3.2, U4.9 (RA2)
TXD: J2.1, U4.15 (PGEC3/5VT/RB6)
~MCLR: J1.1, R4.1, U4.1 (~MCLR)

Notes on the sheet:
Control Trims
Power Supply
Radio
Status LED
MCU
Mounting Holes and Power Flags
Reset Buttons
Controls
Program and Debug
Transmitter

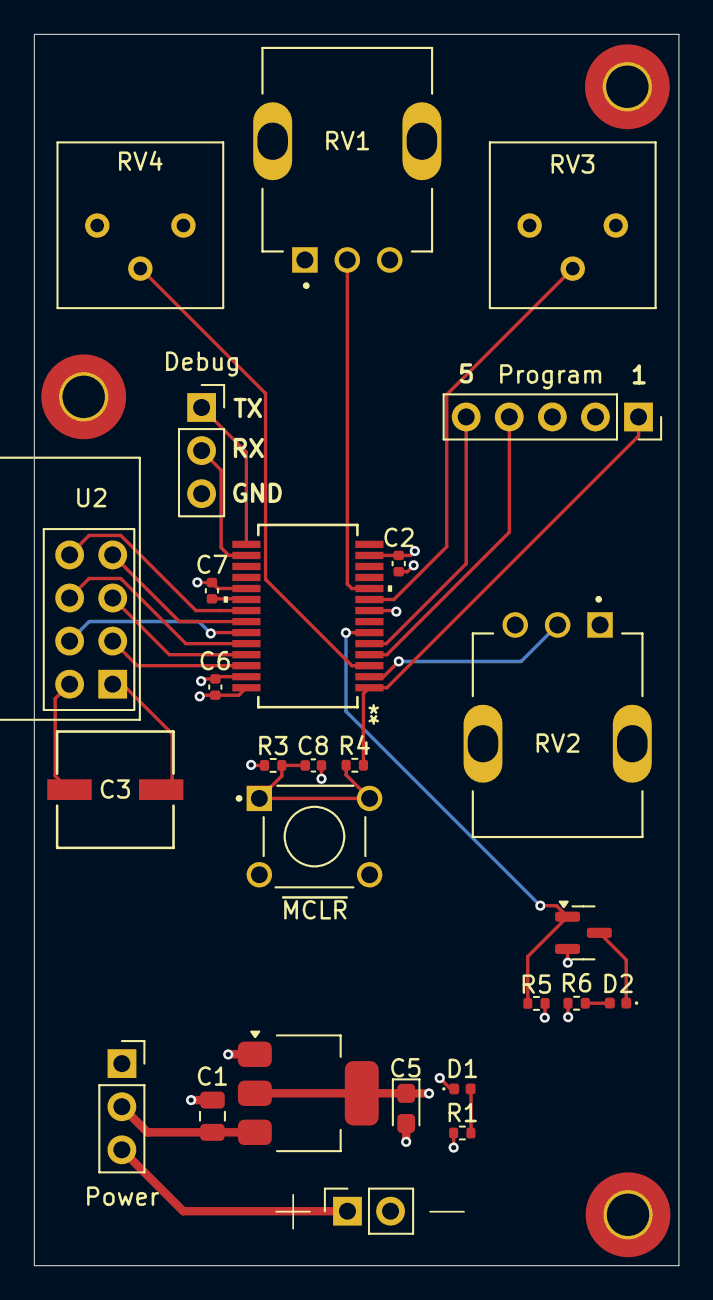
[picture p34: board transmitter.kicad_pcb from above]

Board: 4 copper layers, 38.0 x 72.6 mm, 30 parts (0 on the bottom side), 25 nets.

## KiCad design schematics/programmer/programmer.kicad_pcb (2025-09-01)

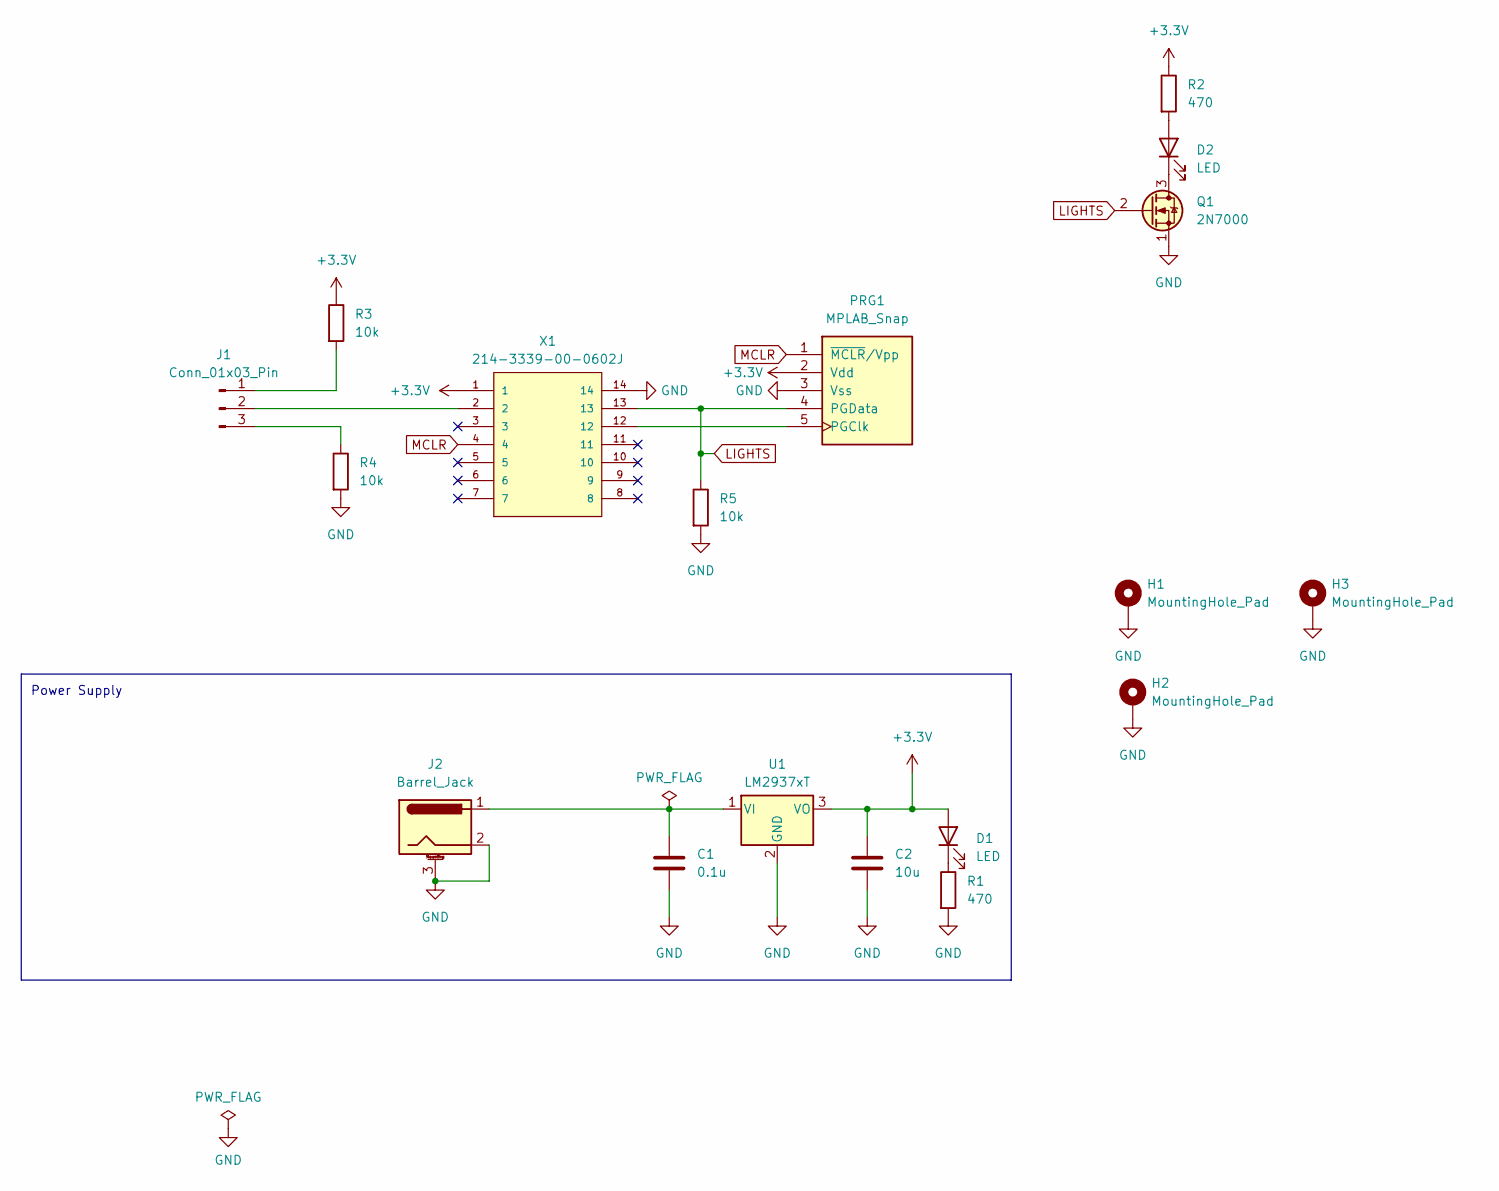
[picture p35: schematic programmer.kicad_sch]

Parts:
C1: 0.1u; CP_Radial_D5.0mm_P2.50mm
C2: 10u; CP_Radial_D5.0mm_P2.50mm
D1, D2: LED; LED_D5.0mm
H1, H2, H3: MountingHole_Pad; MountingHole_2.5mm_Pad_TopBottom
J1: Conn_01x03_Pin; PinSocket_1x03_P2.54mm_Vertical
J2: Barrel_Jack; BarrelJack_Horizontal
PRG1: MPLAB_Snap; PinSocket_1x08_P2.54mm_Vertical
Q1: 2N7000; TO-92_Inline_Wide
R1, R2: 470; R_Axial_DIN0204_L3.6mm_D1.6mm_P7.62mm_Horizontal
R3, R4, R5: 10k; R_Axial_DIN0204_L3.6mm_D1.6mm_P7.62mm_Horizontal
U1: LM2937xT; TO-220-3_Horizontal_TabDown
X1: 214-3339-00-0602J; 3M_214-3339-00-0602J

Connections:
+3.3V: C2.1, D1.2 (A), PRG1.2 (Vdd), R2.1, R3.1, U1.3 (VO), X1.1
GND: C1.2, C2.2, H1.1, H2.1, H3.1, J2.2, J2.3 (MountPin), PRG1.3 (Vss), Q1.1 (S), R1.2, R4.2, R5.2, U1.2 (GND), X1.14
LIGHTS: PRG1.4 (PGData), Q1.2 (G), R5.1, X1.13
MCLR: PRG1.1 (~MCLR/Vpp), X1.4
unnamed: D1.1 (K), R1.1
unnamed: D2.2 (A), R2.2
unnamed: D2.1 (K), Q1.3 (D)
unnamed: J1.1, R3.2
unnamed: J1.2, X1.2
unnamed: J1.3, R4.1
unnamed: PRG1.5 (PGClk), X1.12
unnamed: C1.1, J2.1, U1.1 (VI)

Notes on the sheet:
Power Supply

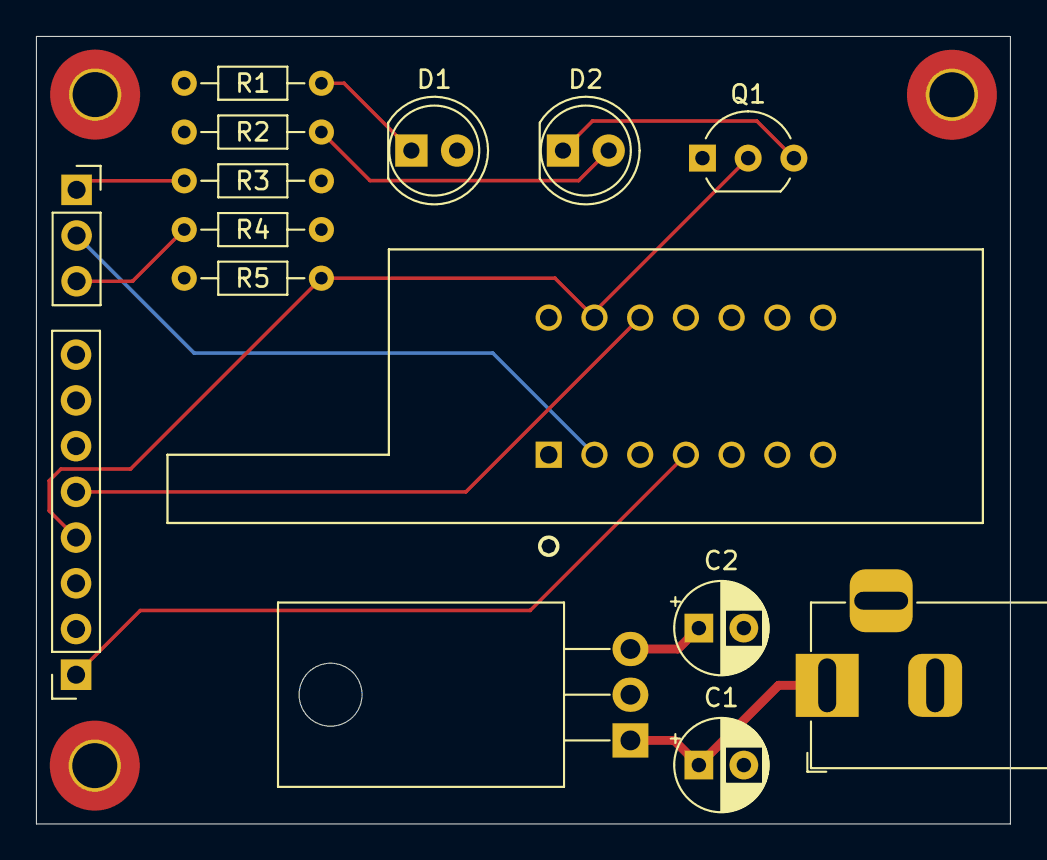
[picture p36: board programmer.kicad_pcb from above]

Board: 4 copper layers, 54.1 x 43.7 mm, 18 parts (0 on the bottom side), 12 nets.

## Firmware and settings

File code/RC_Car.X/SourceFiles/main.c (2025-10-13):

#include <stdio.h>
#include <stdlib.h>
#include <xc.h>
#include "stdbool.h"
#include "../HeaderFiles/TransmitService.h"
#include "string.h"

#pragma config WDTE = OFF           // Watchdog Timer Enable bit (WDT disabled)
#pragma config FEXTOSC = OFF        // External Oscillator mode selection
#pragma config RSTOSC = HFINT1      // Power-up default value for COSC (HFINTOSC with HFFRQ = 1 MHz and CDIV = 1:1)
#pragma config WDTE = OFF           // Watchdog Timer Enable
#pragma config MCLRE = ON           // Master Clear Enable

#define CHANNEL				42
#define ADDRESS_WIDTH		5
#define RADIO_ID			0x01

// radio type defaults to be receiver
Radio_t radioType = RECEIVER;
// address of receiver and transmitter
uint8_t address[] = {0x30, 0x30, 0x30, 0x31, 0x31};
// state for running the state machine
State_t currentState;
// value of LED
bool val = true;
// previous spinning direction of motor
bool prevSpinDir = true;
// current spinning direction of motor
bool spinDir;

// reuse these arrays for sending and receiving data via SPI
uint8_t bytes[7];
uint8_t result[7];

int main(int argc, char** argv) {
    // LED/LIGHT setup
    // configure RA0 (pin 13) as digital output
	TRISAbits.TRISA0 = 0;
    // set as default low
	LATAbits.LATA0 = 0;
    
    // receiver/transmitter selection setup
    // configure RA5 (pin 2) as digital input
	TRISAbits.TRISA5 = 1;
    // disable analog input
    ANSELAbits.ANSA5 = 0;
    // check if radio type should be transmitter
    // if RA5 is HIGH then radio is a transmitter
    // if RA5 is LOW then radio is a receiver
	if (PORTAbits.RA5) {
		radioType = TRANSMITTER;
	}
    
    if (radioType == TRANSMITTER) {
        for (uint8_t i = 0; i < 10; i++) {
            delay(1000);
            LATAbits.LATA0 = 1;
            delay(1000);
            LATAbits.LATA0 = 0;
        }
    } else if (radioType == RECEIVER) {
        for (uint8_t i = 0; i < 3; i++) {
            delay(10000);
            LATAbits.LATA0 = 1;
            delay(10000);
            LATAbits.LATA0 = 0;
        }
    }
    
    // radio CE setup
    if (radioType == TRANSMITTER) {
        // configure RA2 (pin 11) as digital output
        TRISAbits.TRISA2 = 0;
    } else if (radioType == RECEIVER) {
        // configure RC5 (pin 5) as digital output
        TRISCbits.TRISC5 = 0;
    }
    // set radio enable as default low
	ce(radioType, LOW);
    
    // radio IRQ setup
    if (radioType == TRANSMITTER) {
        // configure RC2 (pin 8) as digital input
        TRISCbits.TRISC2 = 1;
        // disable analog input
        ANSELCbits.ANSC2 = 0;
    } else if (radioType == RECEIVER) {
        // configure RA1 (pint 12) as digital input
        TRISAbits.TRISA1 = 1;
        // disable analog input
        ANSELAbits.ANSA1 = 0;
    }
        
    
    // set up SPI
    setupSPI(radioType);
    
    // start radio
    bool radioStarted = true;    
    if (StartRadio(CHANNEL, PAYLOAD_SIZE, radioType)) {
        radioStarted = true;
    } else {
        // radio didn't start successfully
        // blink LED to indicate error
        while (1) {
            LATAbits.LATA0 = val;
            val = ~val;
            delay(10000);
        }
    }

    // if radio as started correctly and radio type is receiver
    // then configure radio and microcontroller as a receiver
    // otherwise configure radio and microcontroller as a transmitter
    if (radioStarted && radioType == RECEIVER) {
        configureRX(address);
        // set initial state
        currentState = READ_RX;
    } else if (radioStarted && radioType == TRANSMITTER) {
        configureTX(address);
        // set initial state
        currentState = COLLECT_ADC_DATA;
        ADCON0bits.GO_nDONE = 1;
    }
    
    // run main state machine
    while (1) {
        switch (currentState) {
            
            // first three states are for the controller only
            // need to collect ADC data from the three potentiometers on the board
            case COLLECT_ADC_DATA: {
                if (!ADCON0bits.GO_nDONE) {
                    // cycle through the three pots
                    if (ADCON0bits.CHS == 0x14) {
                        // store high and low byte into the bytes array
                        bytes[0] = ADRESH;
                        bytes[1] = ADRESL;
                        // switch to next ADC input pin on next ADC conversion
                        ADCON0bits.CHS = 0x13;
                    } else if (ADCON0bits.CHS == 0x13) {
                        bytes[2] = ADRESH;
                        bytes[3] = ADRESL;
                        ADCON0bits.CHS = 0x01;
                    } else if (ADCON0bits.CHS == 0x01) {
                        bytes[4] = ADRESH;
                        bytes[5] = ADRESL;
                        ADCON0bits.CHS = 0x14;
                        // if the controls have changed since the last conversion
                        // then transmit; otherwise repeat the process in this state
                        if (controlsChanged(bytes)) {
                            packagePayload(RADIO_ID, bytes);
                            currentState = TRANSMIT_ADC_DATA;
                            
                        }
                    }
                    ADCON0bits.GO_nDONE = 1;
                }
                break;
            }

            // send data to nRF24L01 via SPI bus and transmit
            case TRANSMIT_ADC_DATA: {
                sendNOP(result);
                transmitPayload(result[0]);
                currentState = CLEAR_INTERRUPT;
                break;
            }
            
            // checks for interrupt to signify when transmission is done
            case CLEAR_INTERRUPT: {
                if (!PORTCbits.RC2) {
                    LATAbits.LATA0 = 1;
                    delay(1000);
                    LATAbits.LATA0 = 0;
                    delay(1000);
                    // get interrupt type 
                    sendNOP(result);
                    // clear interrupt so nRF24L01 can transmit again
                    bytes[0] = W_REGISTER | SPI_STATUS;
                    bytes[1] = 0x70;
                    while (1) {
                        SendSPI(bytes, result, 2);
                        sendNOP(result);
                        if (!(result[0] & 0x70)) {
                            break;
                        }
                    }
                    currentState = DONE;
                }
                break;
            }

            // starts next ADC conversion
            case DONE: {
                currentState = COLLECT_ADC_DATA;
                ADCON0bits.GO_nDONE = 1;
                break;
            }

            // final states are for the receiver
            // read data from the nRF24L01 when it signifies there is data ready
            case READ_RX: {
                // checks for IRQ line to be low
                if (!PORTAbits.RA1) {
                    LATAbits.LATA0 = 1;
                    delay(1000);
                    LATAbits.LATA0 = 0;
                    delay(1000);
                    // once low checks for type of interrupt
                    sendNOP(result);
                    // if interrupt is data ready (0x40) then begin data collection process
                    if (result[0] & 0x40) {
                        currentState = UPDATE_CONTROLS;
                    }
                    // clear interrupts
                    bytes[0] = W_REGISTER | SPI_STATUS;
                    bytes[1] = 0x70;
                    SendSPI(bytes, result, 2);
                }
                break;
            }
            
            // gets data from nRF24L01 and updates servo and motor
            case UPDATE_CONTROLS: {
                // collect data from nRF24L01 and check if validity
                bool validData = readRXFIFO(result);
                // if data is uncorrupted and coming from the right source then update
                if (validData && result[1] == RADIO_ID) {
                    // convert motor and servo data to proper data type
                    uint16_t motorSpeed = (uint16_t)((result[2] << 8) | result[3]);
                    uint16_t servoPos = (uint16_t)((result[4] << 8) | result[5]);
                    // convert servo data to a 1ms to 2ms format
                    servoPos = (servoPos * 15 + 15345) / 1023;
                    // convert motor data such that 0 is full reverse, 512 is 
                    // stopped, and 1023 is full forward
                    if (motorSpeed > 512) {
                        motorSpeed -= 512;
                        spinDir = true;
                    } else {
                        motorSpeed = 512 - motorSpeed;
//                        motorSpeed = 0;
                        spinDir = false;
                    }
                    // disable motor pwm line
                    PWM5CONbits.PWM5EN = 0;
                    // check if motor spin direction has changed
                    if (prevSpinDir != spinDir) {
                        // if changed then swap pin mapping
                        if (spinDir) {
                            RC2PPS = 0b00010;
                            RC4PPS = 0b00000;
                            LATCbits.LATC4 = 0;
                        } else {
                            RC2PPS = 0b00000;
                            RC4PPS = 0b00010;
                            LATCbits.LATC2 = 0;
                        }
                        // update motor spinning direction
                        prevSpinDir = spinDir;
                    }
                    
                    // update motor PWM speed
                    PWM5DCL = (uint8_t)(motorSpeed << 6);
                    PWM5DCH = (uint8_t)(motorSpeed >> 2);
                    
                    // update servo PWM speed
                    PWM6DCL = (uint8_t)(servoPos << 6);
                    PWM6DCH = (uint8_t)(servoPos >> 2);
                    
                    // re-enable motor PWM
                    PWM5CONbits.PWM5EN = 1;
                }
                // go back to READ_RX state and wait for next command to be ready
                currentState = READ_RX;
                break;
            }
        }
    }
    return 1;
}

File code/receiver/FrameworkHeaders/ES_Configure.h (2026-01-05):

/****************************************************************************
 Module
     ES_Configure.h
 Description
     This file contains macro definitions that are edited by the user to
     adapt the Events and Services framework to a particular application.
 Notes

 History
 When           Who     What/Why
 -------------- ---     --------
 12/19/16 20:19  jec     removed EVENT_CHECK_HEADER definition. This goes with
                         the V2.3 move to a single wrapper for event checking
                         headers
  10/11/15 18:00 jec     added new event type ES_SHORT_TIMEOUT
  10/21/13 20:54 jec     lots of added entries to bring the number of timers
                         and services up to 16 each
 08/06/13 14:10 jec      removed PostKeyFunc stuff since we are moving that
                         functionality out of the framework and putting it
                         explicitly into the event checking functions
 01/15/12 10:03 jec      started coding
*****************************************************************************/

#ifndef ES_CONFIGURE_H
#define ES_CONFIGURE_H

/****************************************************************************/
// The maximum number of services sets an upper bound on the number of
// services that the framework will handle. Reasonable values are 8 and 16
// corresponding to an 8-bit(uint8_t) and 16-bit(uint16_t) Ready variable size
#define MAX_NUM_SERVICES 16

/****************************************************************************/
// This macro determines that nuber of services that are *actually* used in
// a particular application. It will vary in value from 1 to MAX_NUM_SERVICES
#define NUM_SERVICES 1

/****************************************************************************/
// These are the definitions for Service 0, the lowest priority service.
// Every Events and Services application must have a Service 0. Further
// services are added in numeric sequence (1,2,3,...) with increasing
// priorities
// the header file with the public function prototypes
#define SERV_0_HEADER "ReceiverService.h"
// the name of the Init function
#define SERV_0_INIT InitReceiverService
// the name of the run function
#define SERV_0_RUN RunReceiverService
// How big should this services Queue be?
#define SERV_0_QUEUE_SIZE 5

/****************************************************************************/
// The following sections are used to define the parameters for each of the
// services. You only need to fill out as many as the number of services
// defined by NUM_SERVICES
/****************************************************************************/
// These are the definitions for Service 1
#if NUM_SERVICES > 1
// the header file with the public function prototypes
#define SERV_1_HEADER "TestHarnessService1.h"
// the name of the Init function
#define SERV_1_INIT InitTestHarnessService1
// the name of the run function
#define SERV_1_RUN RunTestHarnessService1
// How big should this services Queue be?
#define SERV_1_QUEUE_SIZE 3
#endif

/****************************************************************************/
// These are the definitions for Service 2
#if NUM_SERVICES > 2
// the header file with the public function prototypes
#define SERV_2_HEADER "TestHarnessService2.h"
// the name of the Init function
#define SERV_2_INIT InitTestHarnessService2
// the name of the run function
#define SERV_2_RUN RunTestHarnessService2
// How big should this services Queue be?
#define SERV_2_QUEUE_SIZE 3
#endif

/****************************************************************************/
// These are the definitions for Service 3
#if NUM_SERVICES > 3
// the header file with the public function prototypes
#define SERV_3_HEADER "TestHarnessService3.h"
// the name of the Init function
#define SERV_3_INIT InitTestHarnessService3
// the name of the run function
#define SERV_3_RUN RunTestHarnessService3
// How big should this services Queue be?
#define SERV_3_QUEUE_SIZE 3
#endif

/****************************************************************************/
// These are the definitions for Service 4
#if NUM_SERVICES > 4
// the header file with the public function prototypes
#define SERV_4_HEADER "TestHarnessService4.h"
// the name of the Init function
#define SERV_4_INIT InitTestHarnessService4
// the name of the run function
#define SERV_4_RUN RunTestHarnessService4
// How big should this services Queue be?
#define SERV_4_QUEUE_SIZE 3
#endif

/****************************************************************************/
// These are the definitions for Service 5
#if NUM_SERVICES > 5
// the header file with the public function prototypes
#define SERV_5_HEADER "TestHarnessService5.h"
// the name of the Init function
#define SERV_5_INIT InitTestHarnessService5
// the name of the run function
#define SERV_5_RUN RunTestHarnessService5
// How big should this services Queue be?
#define SERV_5_QUEUE_SIZE 3
#endif
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

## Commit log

2025-07-04 Begin schematic for rc car
    [schema.kicad_pcb, schema.kicad_sch]
2025-07-12 Update schematic with new microcontroller
    [schema.kicad_sch]
2025-07-19 Update schematic. Remote motor control working
    [schema.kicad_sch]
2025-07-20 Add servo pwm
2025-08-05 Update schematic to use PIC16 from PIC32
    [schema.kicad_pcb, schema.kicad_sch]
2025-08-05 Update schematics 3d models for rendering
    [BH9VPC.step, TS02-66-60-BK-160-LCR-D.STEP, pins.xlsx]
2025-08-07 Add ADC channel init
2025-08-07 Add switch to schema
    [EG1218.step, schema.kicad_pcb, schema.kicad_sch]
2025-08-25 Change pinout on pic16 in schematic
    [schema.kicad_sch]
2025-08-25 Begin transmiter schematic
    [transmitter_schema.kicad_pcb, transmitter_schema.kicad_sch]
2025-08-25 Correct faulty SPI code and add transmitter FSM
    [SPI.c, TransmitService.c, main.c]
2025-08-29 Refactors schematics
    [1825910-6.step, 3386P-1-104LF.STEP, PT01-D115D-B502.step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]
2025-08-29 Remove out of data schematics
    [BH9VPC.step, EG1218.step, PT01-D115D-B502.step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]
2025-08-29 Remove unnecessary devices
    [transmitter.kicad_pcb, transmitter.kicad_sch]
2025-08-29 Add schematic titles
    [receiver.kicad_sch, transmitter.kicad_sch]
2025-08-29 Create pin description document for TX and RX
    [pin_description.xlsx]
2025-08-29 Change mcu type select to be pull down for RX board
    [pin_description.xlsx, receiver.kicad_pcb, receiver.kicad_sch]
2025-08-29 Add pull up for TX mcu select
    [pin_description.xlsx, transmitter.kicad_pcb, transmitter.kicad_sch]
2025-08-30 Working motor and servo driver code
    [pin_description.xlsx]
2025-08-31 Remove rear LEDs and move hbridge away from radio
    [receiver.kicad_pcb]
2025-08-31 Rearrange for more room for screws
    [receiver.kicad_pcb]
2025-09-01 Created programming board. Schematic needs cleaning up
    [TFXTDOL14-Assy-Down.step, TFXTDOL14-Assy-Up.step, programmer.kicad_pcb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]
2025-09-01 Add pull down resistor
    [programmer.kicad_pcb]
2025-09-01 Add pull down resistor for LED control on receiver board
    [receiver.kicad_pcb, receiver.kicad_sch]
2025-09-01 Add pull down for lights on transmitter board
    [transmitter.kicad_pcb, transmitter.kicad_sch, transmitter.step]
2025-09-02 Remove trim pot, seems unnecessary
    [transmitter.kicad_pcb, transmitter.kicad_sch, transmitter.step]
2025-09-14 Begin master bill of materials
    [parts_list.xlsx]
2025-09-14 Remove programing ports and reset btn from final boards
    [9V-battery.stp, BH9VPC.STEP, receiver.kicad_pcb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]
2025-09-22 Updated switch with better 3d model
    [receiver.kicad_pcb, receiver.step, switch v1.step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]
2025-09-24 Add trim pot to transmitter
    [transmitter.kicad_pcb, transmitter.kicad_sch, transmitter.step]
2025-09-25 Update schematic backups
2025-09-25 Create gerber files and order
    [receiver-B_Cu.gbr, receiver-B_Mask.gbr, receiver-B_Paste.gbr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]
2025-10-04 Make receiver schematic more readable and add images
    [receiver.kicad_sch, transmitter.kicad_pcb, transmitter.step]
2025-10-04 Crop receiver schematic
2025-10-04 Update schematics and their images
    [receiver.kicad_sch, transmitter.kicad_sch]
2025-10-04 Update BOM for transmitter
    [receiver.kicad_sch, transmitter.kicad_sch]
2025-10-07 Update images
    [bom.csv, transmitter.kicad_sch]
2025-12-23 Update bom
    [bom.csv]
2026-01-05 Mark changes on kicad
    [receiver.kicad_sch, transmitter.kicad_sch]
